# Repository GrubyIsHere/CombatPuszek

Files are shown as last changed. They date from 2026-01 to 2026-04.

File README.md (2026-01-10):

# CombatPuszek
Fancy combat-type robot with huge saw on top.

Angled version

Flattop version

## Features
*   ESP32-based remote control system.
*   All-around horizontal saw, up to 250mm in diameter.
*   3lbs (1.36kg) weight category.
*   Two drive configurations: wheels or soft tracks.
*   Swappable motor drivers, main ESC, and even main ESP32 module. 
*   Powered by 3S LiPO.

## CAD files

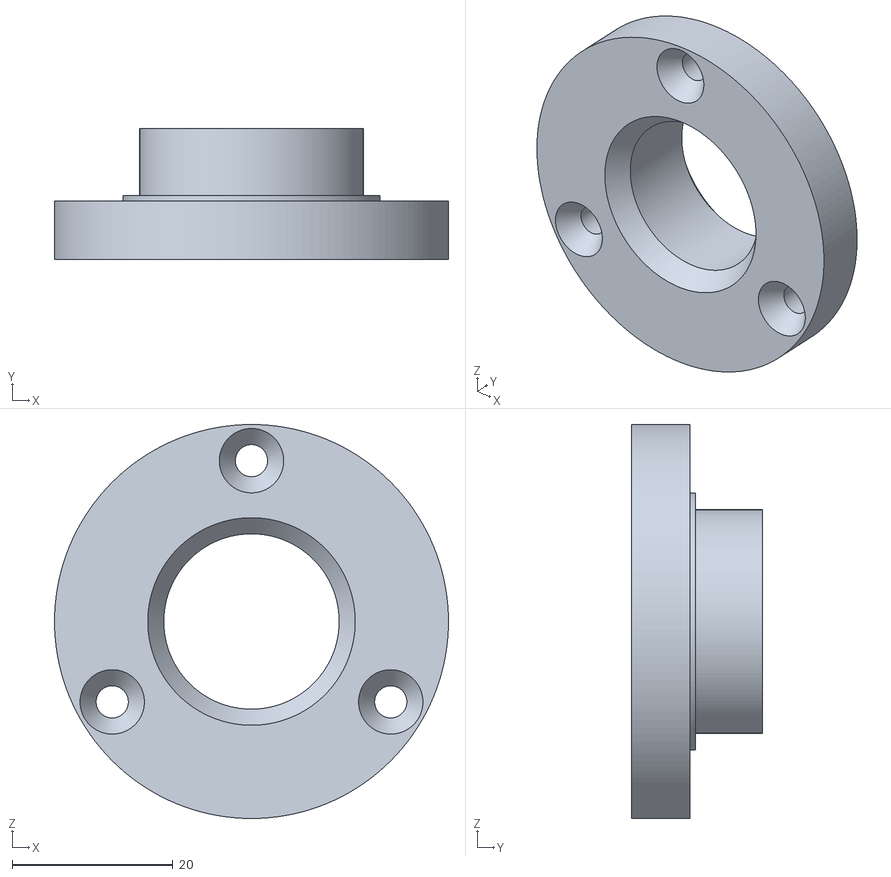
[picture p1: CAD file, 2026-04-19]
Mechanicals/mocowania_piły/nextgen_sidemount_alt_32mm - docisk_piły_fullprzelot.stl
49.0 x 16.2 x 49.0

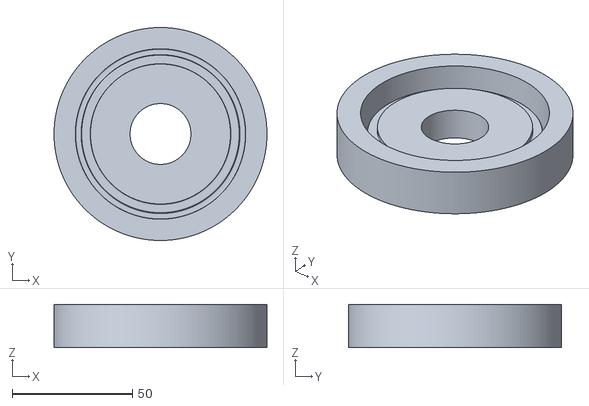
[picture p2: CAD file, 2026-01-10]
Mechanicals/koła_fi34/gąska dla kół fi34/baza_fi70,8.stl
88.5 x 88.5 x 18.0

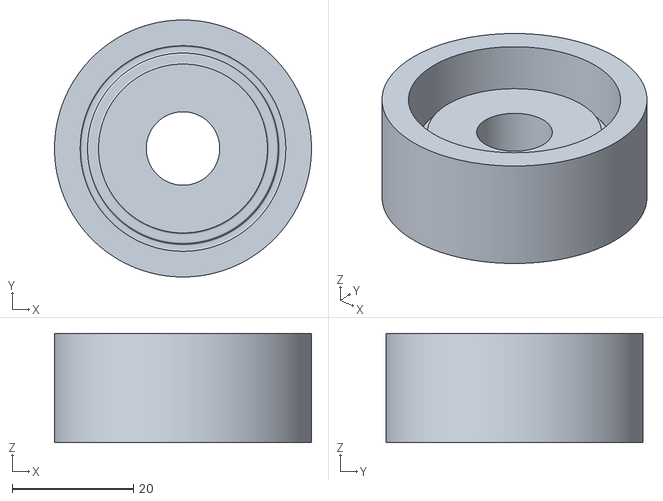
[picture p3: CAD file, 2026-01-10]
Mechanicals/koła_fi34/opona dla kół fi34/baza_fi34.stl
42.4 x 42.4 x 18.0

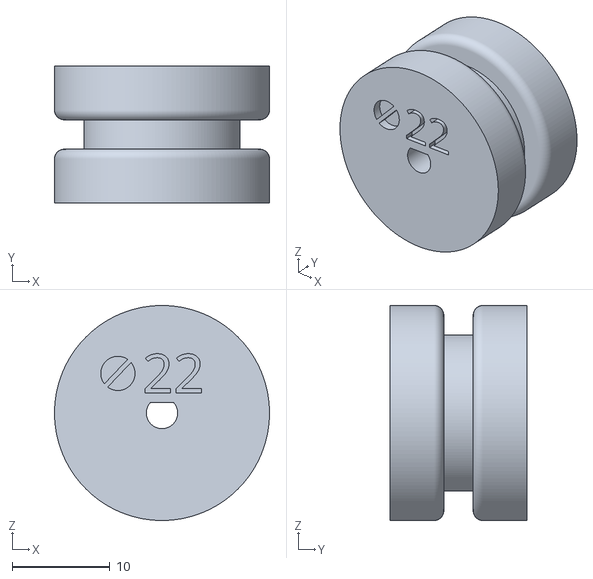
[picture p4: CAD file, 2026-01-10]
Mechanicals/koła_inne/puszkoło_fi22.stl
22.0 x 14.0 x 22.0

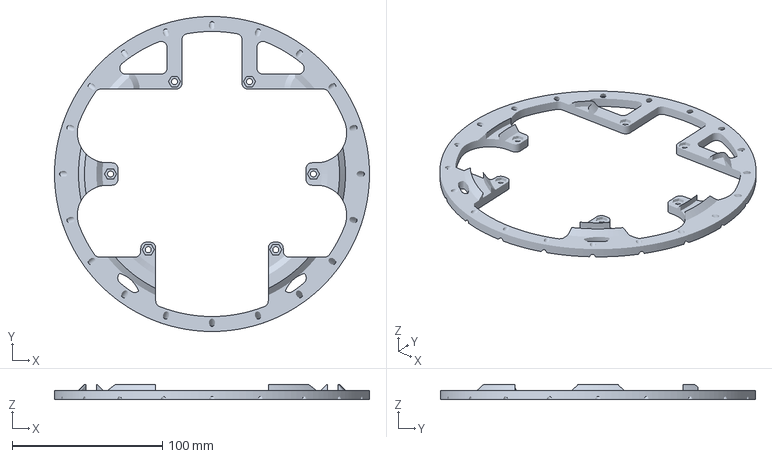
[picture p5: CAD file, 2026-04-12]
Mechanicals/kryzy/kryza_płaska_nextgen - dół.3mf
210.0 x 210.0 x 10.0 mm

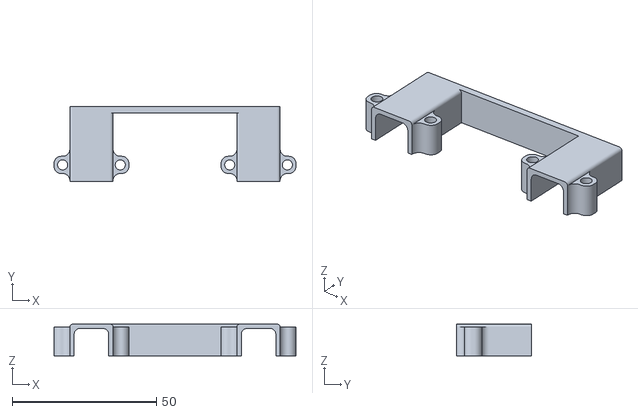
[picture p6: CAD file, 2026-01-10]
Mechanicals/mocowania_silników/doubleBracket_solid.stl
84.0 x 26.0 x 11.0

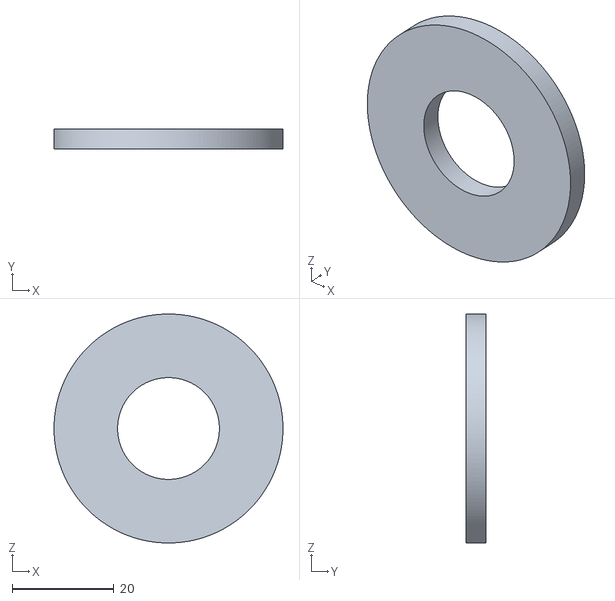
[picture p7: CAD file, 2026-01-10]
Mechanicals/podkładka_20x45x4mm.stl
45.0 x 4.00 x 45.0

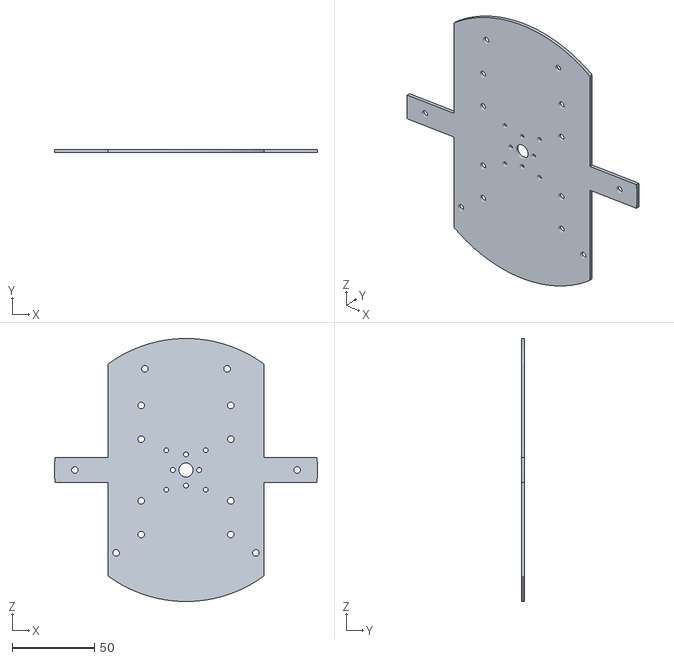
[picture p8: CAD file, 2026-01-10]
Mechanicals/spody/matryca_spodu_wersja_lekka.stl
160.0 x 2.00 x 160.0

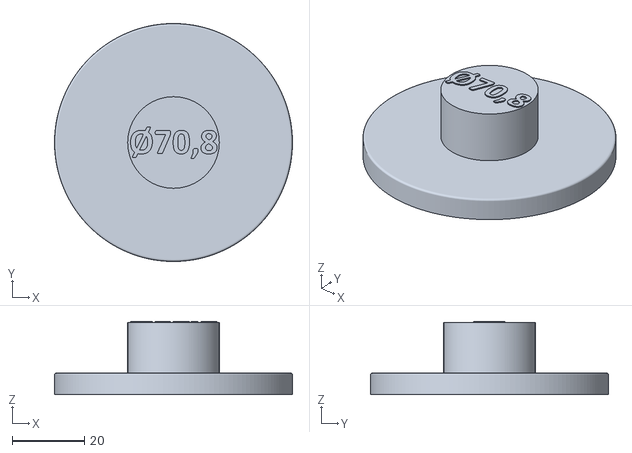
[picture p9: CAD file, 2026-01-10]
Mechanicals/koła_fi34/gąska dla kół fi34/korek_fi70,8.stl
65.7 x 65.7 x 20.3

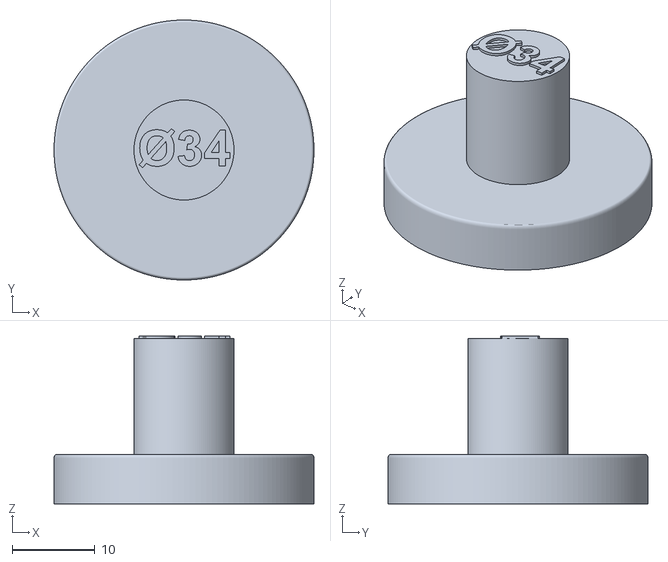
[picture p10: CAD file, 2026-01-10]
Mechanicals/koła_fi34/opona dla kół fi34/korek_fi34.stl
31.5 x 31.5 x 20.3

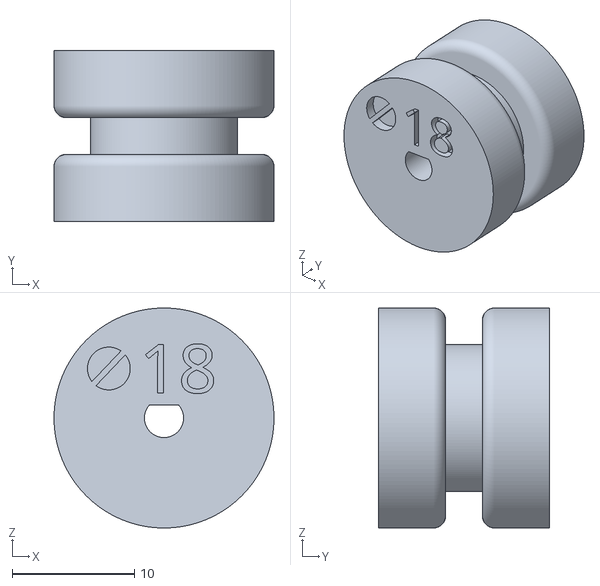
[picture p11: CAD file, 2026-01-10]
Mechanicals/koła_inne/puszkoło_fi18.stl
18.0 x 14.0 x 18.0

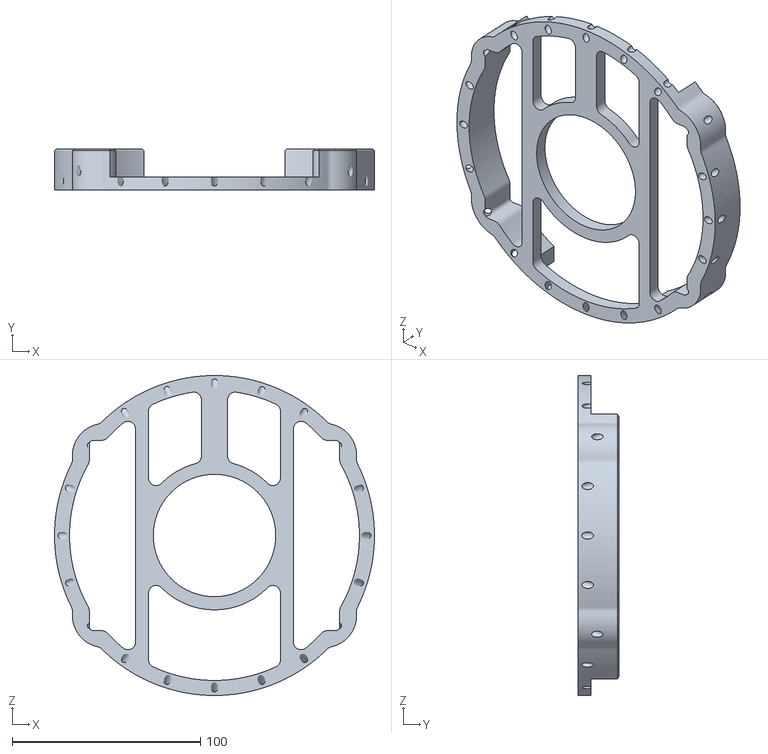
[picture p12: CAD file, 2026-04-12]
Mechanicals/kryzy/kryza_płaska_nextgen - góra.stl
170.0 x 22.0 x 170.0

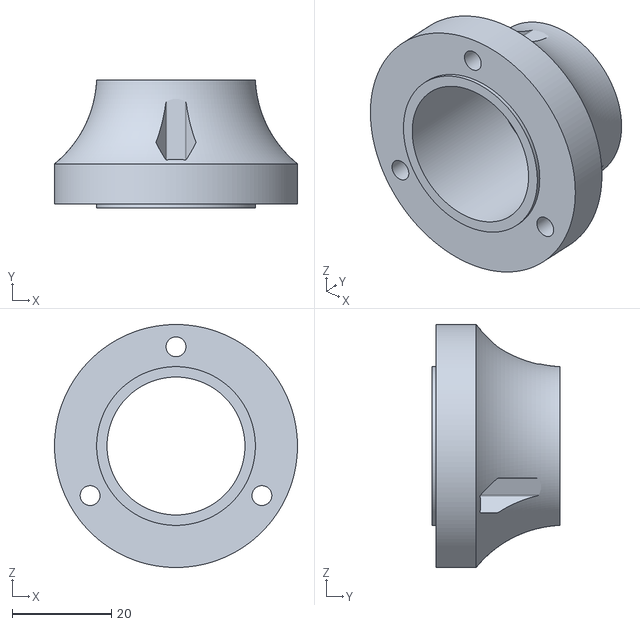
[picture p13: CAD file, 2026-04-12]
Mechanicals/mocowania_piły/nextgen_sidemount_32mm - łoże_piły.stl
49.0 x 25.8 x 49.0

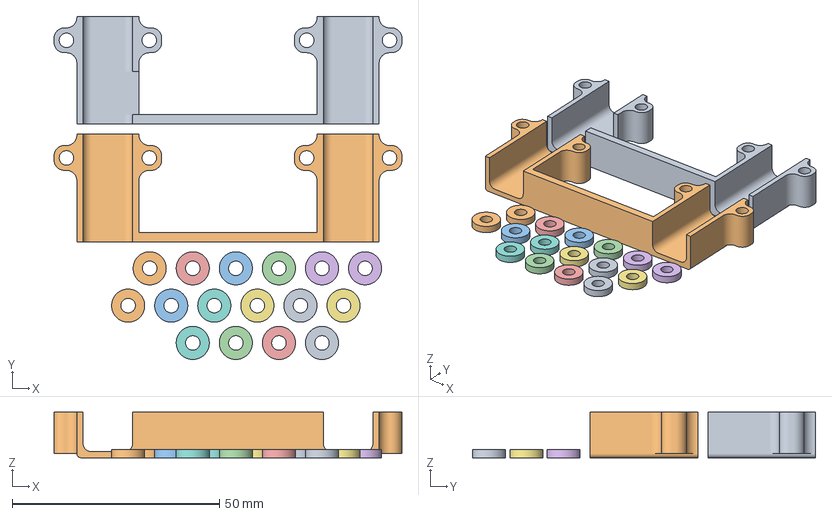
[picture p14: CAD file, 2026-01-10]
Mechanicals/mocowania_silników/mocowania_silników.3mf
84.0 x 82.8 x 11.0 mm
doubleBracket_cutted.stl
doubleBracket_solid.stl
podkładka_3.5x8x2mm.stl x 16

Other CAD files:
Mechanicals/podkładka_3.5x8x2mm.stl
Mechanicals/spody/puszek_blacha_plasticzanowa_gruba.step
Mechanicals/koła_inne/fi34.stl
Mechanicals/kryzy/kątokryza_13st.stl
Mechanicals/koła_inne/fi28.stl
Mechanicals/koła_inne/puszkoło_fi20.stl
Mechanicals/koła_inne/puszkoło_fi24.stl
Mechanicals/kryzy/kryza_płaska_OLD.stl
Mechanicals/kryzy/kryza_płaska_nextgen - dół.stl
Mechanicals/kryzy/kątokryza_10st.stl
Mechanicals/mocowania_piły/kątownik_piły_10st.stl
Mechanicals/mocowania_piły/kątownik_piły_13st.stl
Mechanicals/mocowania_piły/mocowanie_piły_górnodolne_multicentra_20mm.stl
Mechanicals/mocowania_piły/mocowanie_piły_górnodolne_multicentra_32mm.stl
Mechanicals/mocowania_silników/doubleBracket_cutted.stl
Mechanicals/spody/puszek_blacha_plasticzanowa_lekka.step

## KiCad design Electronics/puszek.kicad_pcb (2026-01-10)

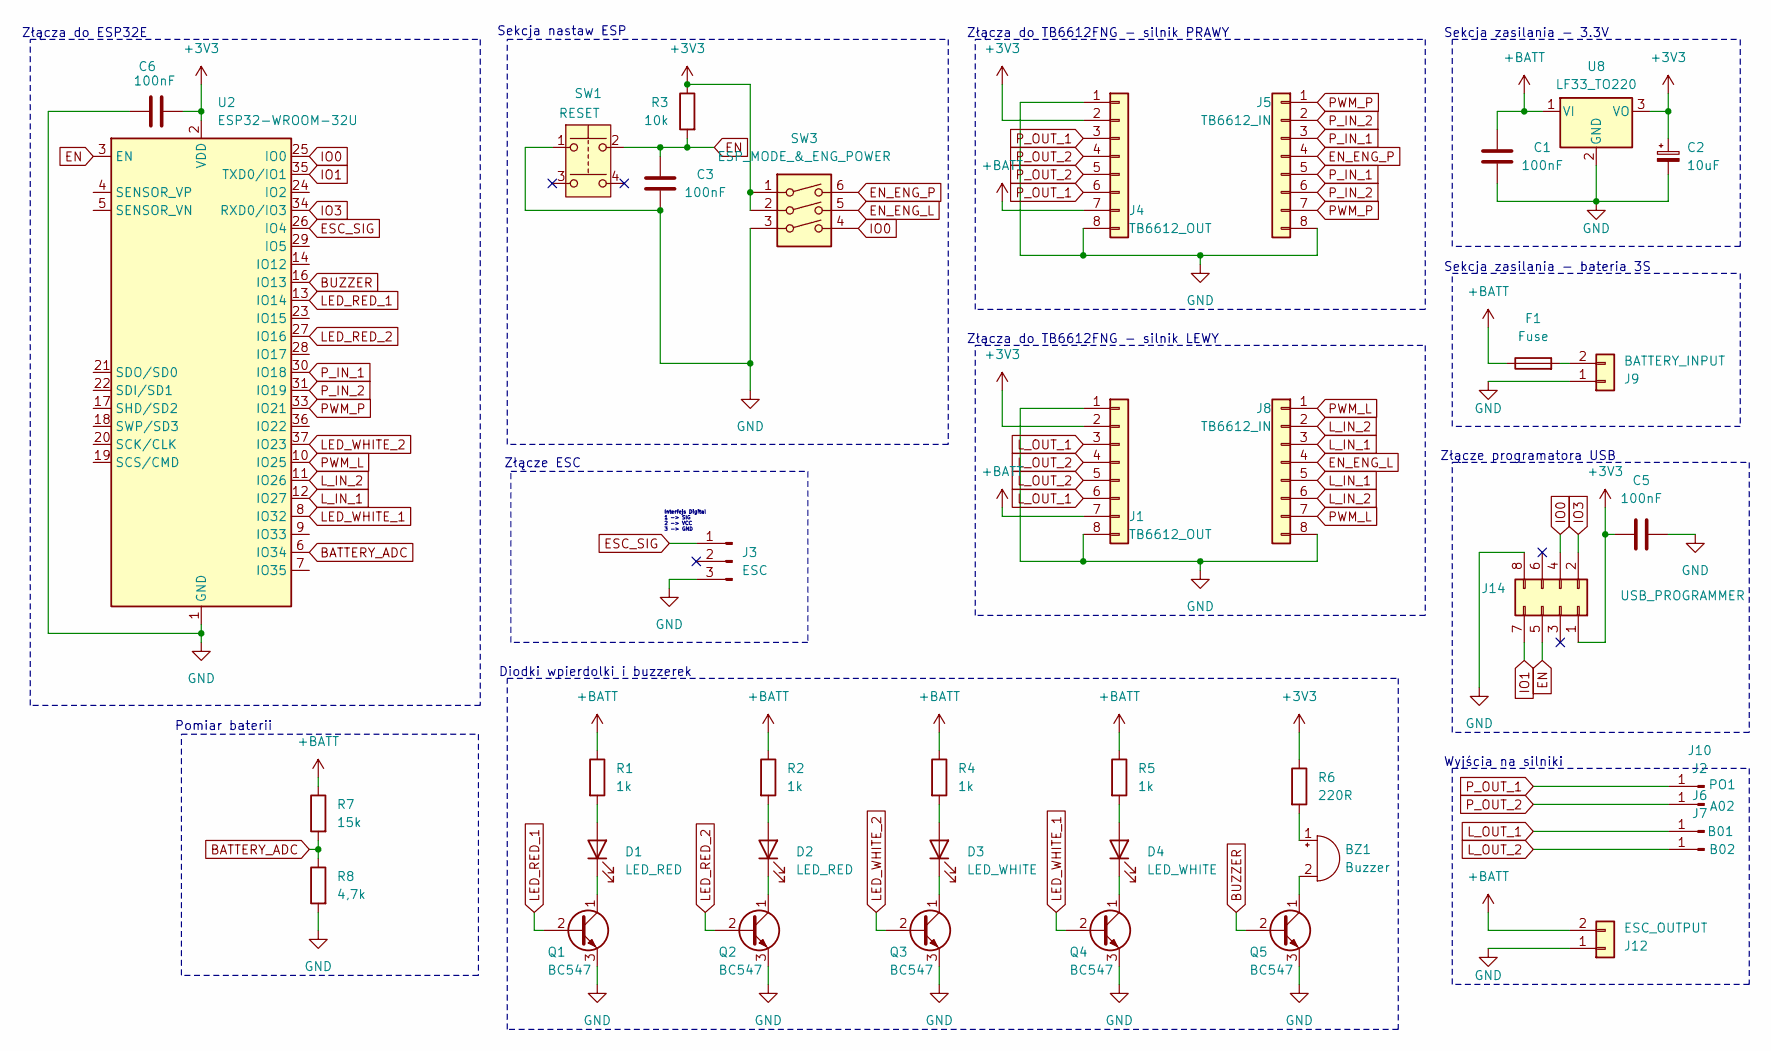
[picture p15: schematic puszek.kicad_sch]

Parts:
BZ1: Buzzer; Buzzer_12x9.5RM7.6
C1, C3, C5, C6: 100nF; C_0603_1608Metric
C2: 10uF; CP_Radial_D5.0mm_P2.50mm
D1, D2: LED_RED; LED_D5.0mm
D3, D4: LED_WHITE; LED_D5.0mm
F1: Fuse; Fuse_Littelfuse_395Series
J1, J4: TB6612_OUT; PinHeader_1x08_P2.54mm_Vertical
J2: A02; PinHeader_1x01_P2.54mm_Vertical
J3: ESC; PinHeader_1x03_P2.54mm_Vertical
J5, J8: TB6612_IN; PinHeader_1x08_P2.54mm_Vertical
J6: B01; PinHeader_1x01_P2.54mm_Vertical
J7: B02; PinHeader_1x01_P2.54mm_Vertical
J9: BATTERY_INPUT; AMASS_XT60-F_1x02_P7.20mm_Vertical
J10: PO1; PinHeader_1x01_P2.54mm_Vertical
J12: ESC_OUTPUT; AMASS_XT60-F_1x02_P7.20mm_Vertical
J14: USB_PROGRAMMER; PinHeader_2x04_P2.54mm_Vertical
Q1, Q2, Q3, Q4, Q5: BC547; TO-92_Inline
R1, R2, R4, R5: 1k; R_0603_1608Metric
R3: 10k; R_0603_1608Metric
R6: 220R; R_0603_1608Metric
R7: 15k; R_0603_1608Metric
R8: 4,7k; R_0603_1608Metric
SW1: RESET; SW_PUSH_6mm_H5mm
SW3: ESP_MODE_&_ENG_POWER; SW_DIP_SPSTx03_Slide_9.78x9.8mm_W7.62mm_P2.54mm
U2: ESP32-WROOM-32U; adapter_ESP32_NEW
U8: LF33_TO220; TO-220-3_Horizontal_TabDown

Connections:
+3V3: C2.1, C5.1, C6.1, J1.2, J4.2, J14.1, R3.1, R6.1, SW3.1, SW3.2, U2.2 (VDD), U8.3 (VO)
+BATT: C1.2, F1.1, J1.7, J4.7, J12.2, R1.1, R2.1, R4.1, R5.1, R7.1, U8.1 (VI)
BATTERY_ADC: R7.2, R8.1, U2.6 (IO34)
BUZZER: Q5.2 (B), U2.16 (IO13)
EN: C3.2, J14.5, R3.2, SW1.2, U2.3 (EN)
EN_ENG_L: J8.4, SW3.5
EN_ENG_P: J5.4, SW3.6
ESC_SIG: J3.1, U2.26 (IO4)
GND: C1.1, C2.2, C3.1, C5.2, C6.2, J1.1, J1.8, J3.3, J4.1, J4.8, J5.8, J8.8, J9.1, J12.1, J14.8, Q1.3 (E), Q2.3 (E), Q3.3 (E), Q4.3 (E), Q5.3 (E), R8.2, SW1.1, SW3.3, U2.1 (GND), U2.15 (GND), U2.38 (GND), U2.39 (GND), U8.2 (GND)
IO0: J14.4, SW3.4, U2.25 (IO0)
IO1: J14.7, U2.35 (TXD0/IO1)
IO3: J14.2, U2.34 (RXD0/IO3)
LED_RED_1: Q1.2 (B), U2.13 (IO14)
LED_RED_2: Q2.2 (B), U2.27 (IO16)
LED_WHITE_1: Q4.2 (B), U2.8 (IO32)
LED_WHITE_2: Q3.2 (B), U2.37 (IO23)
L_IN_1: J8.3, J8.5, U2.12 (IO27)
L_IN_2: J8.2, J8.6, U2.11 (IO26)
L_OUT_1: J1.3, J1.6, J6.1
L_OUT_2: J1.4, J1.5, J7.1
unnamed: BZ1.1 (+), R6.2
unnamed: BZ1.2 (-), Q5.1 (C)
unnamed: D1.2 (A), R1.2
unnamed: D1.1 (K), Q1.1 (C)
unnamed: D2.2 (A), R2.2
unnamed: D2.1 (K), Q2.1 (C)
unnamed: D3.2 (A), R4.2
unnamed: D3.1 (K), Q3.1 (C)
unnamed: D4.2 (A), R5.2
unnamed: D4.1 (K), Q4.1 (C)
unnamed: F1.2, J9.2
PWM_L: J8.1, J8.7, U2.10 (IO25)
PWM_P: J5.1, J5.7, U2.33 (IO21)
P_IN_1: J5.3, J5.5, U2.30 (IO18)
P_IN_2: J5.2, J5.6, U2.31 (IO19)
P_OUT_1: J4.3, J4.6, J10.1
P_OUT_2: J2.1, J4.4, J4.5

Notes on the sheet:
Sekcja zasilania - bateria 3S
Pomiar baterii
Wyjścia na silniki
Interfejs Digital 1 -> SIG 2 -> VCC 3 -> GND
Złącza do TB6612FNG - silnik LEWY
Złącza do ESP32E
Złącze programatora USB
Złącza do TB6612FNG - silnik PRAWY
Sekcja nastaw ESP
Złącze ESC
Sekcja zasilania - 3.3V
Diodki wpierdolki i buzzerek

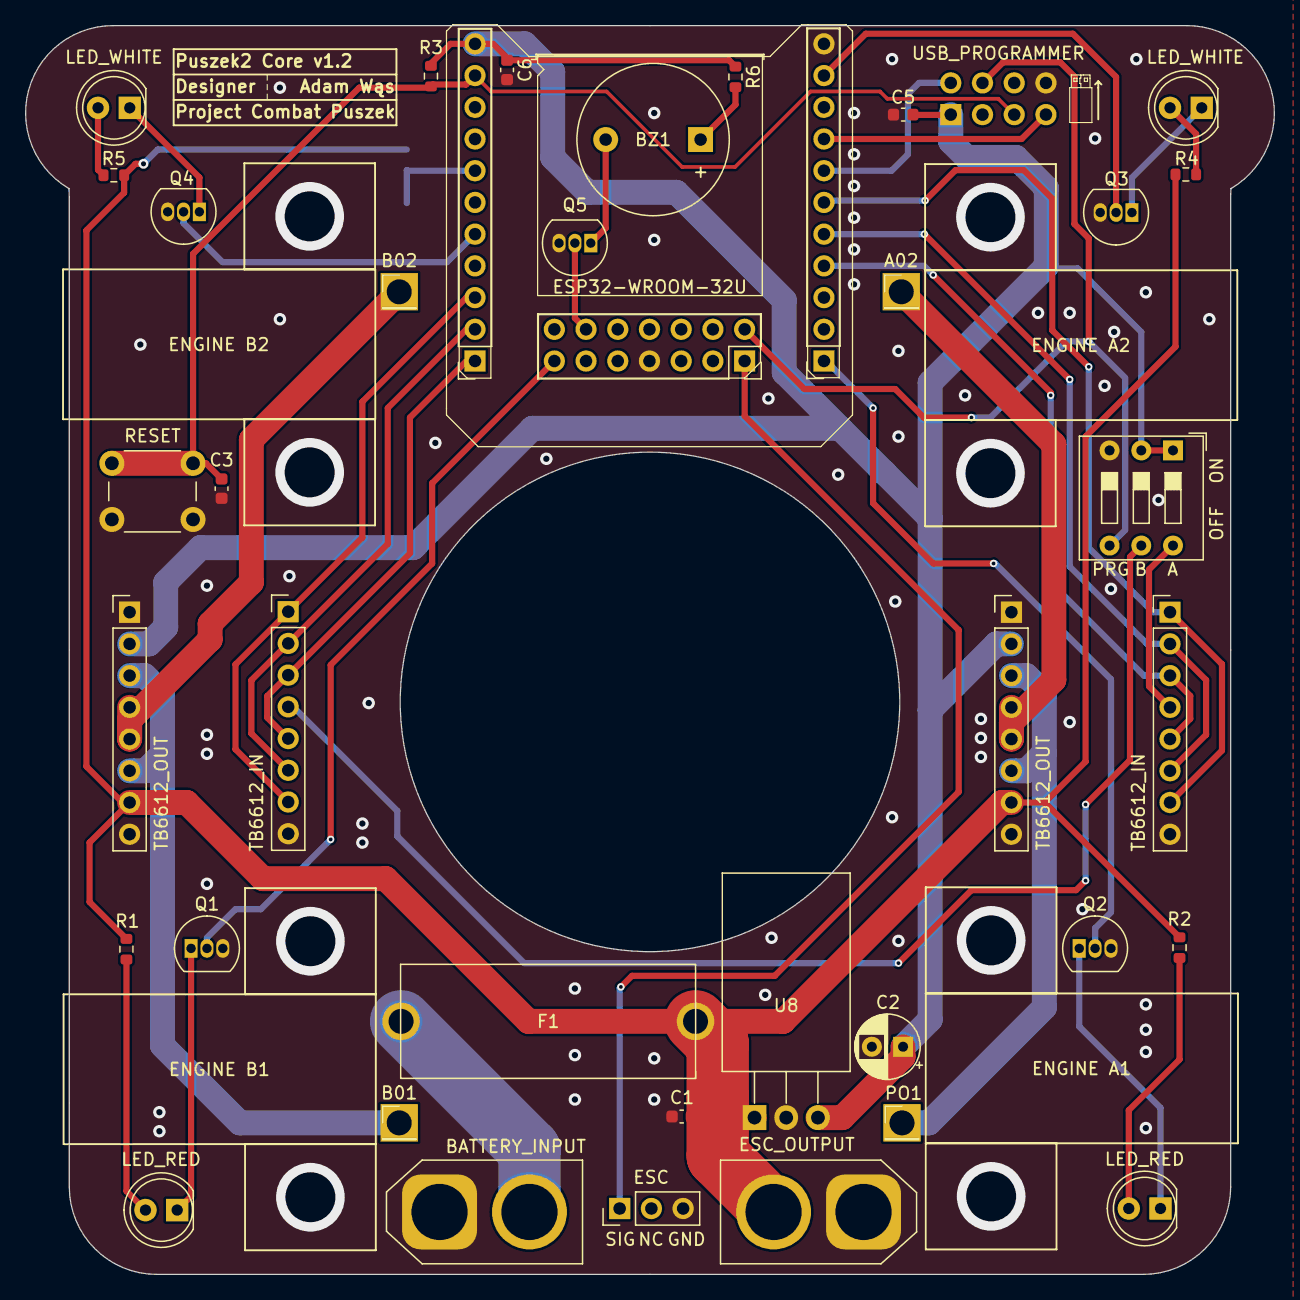
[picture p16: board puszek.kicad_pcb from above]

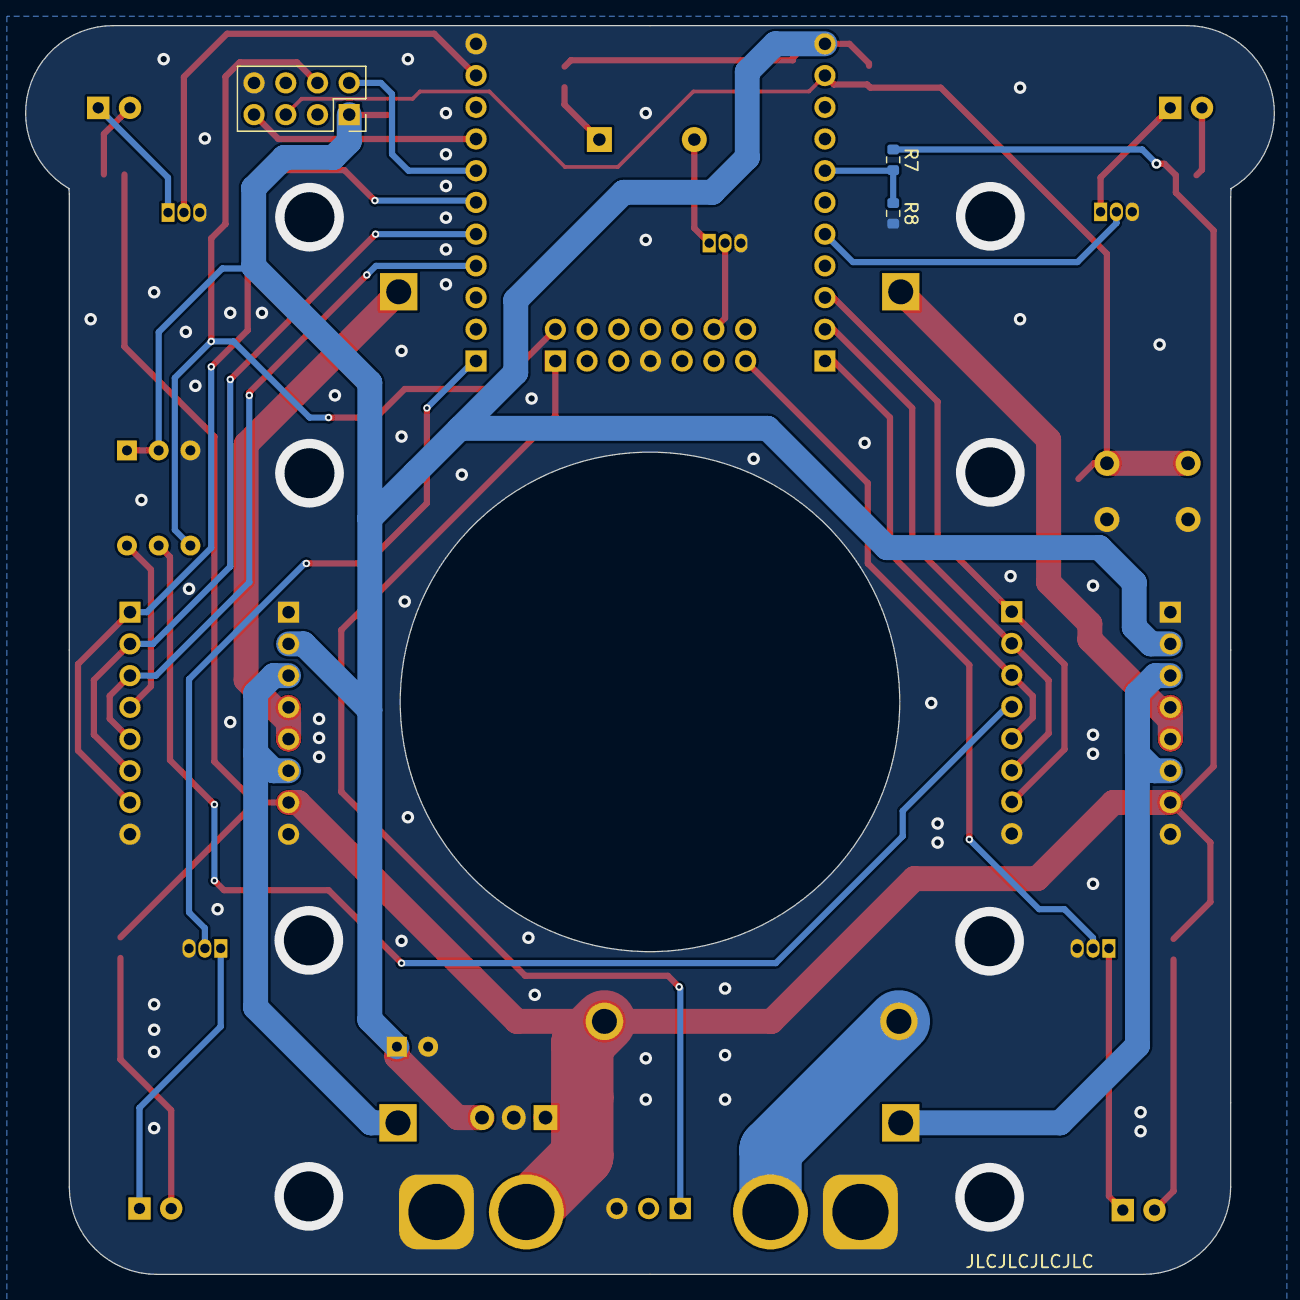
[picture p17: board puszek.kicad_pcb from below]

Board: 2 copper layers, 100.0 x 100.0 mm, 40 parts (2 on the bottom side), 37 nets.

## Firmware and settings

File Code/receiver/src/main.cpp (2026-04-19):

#include <A_Robot.h>
#include <K_ESPNOW.h>
#include <Arduino.h>

K_ESPNOW E;
A_Robot R;

void setup() {
  // Serial Monitor DEBUG
  Serial.begin(115200);
  Serial.println("predone");

  E.Init();

  Serial.println("done");
}

void loop() {

  E.UpdateConnectionState();

  R.ManualControl();

// debug
  Serial.println(E.control.brake);
  Serial.println(E.control.connected);
  Serial.println(E.control.saw);
  Serial.println(E.control.speed_left);
  Serial.println(E.control.speed_right);
  // delay(1000);
}

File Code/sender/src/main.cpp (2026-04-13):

#include <Arduino.h>
#include <K_ESPNOW.h>
#include <S_Buttons.h>

// Complete project details at https://RandomNerdTutorials.com/esp-now-esp8266-nodemcu-arduino-ide/
K_ESPNOW E;
S_Buttons B;

// do timingu połączenia (musi być globalne)
unsigned long lastTime = 0;  
unsigned long interval = 1;

void setup()
{
  E.Init();

  // Serial.begin(115200);
  // Serial.println("done");
}

void loop()
{
  // Serial.println("loopstart");

  if (B.GetState(B.POINTER))
  {
    E.control.speed_left = 100;
  }
  else if (B.GetState(B.RING))
  {
    E.control.speed_left = -100;
  }
  else
  {
    E.control.speed_left = 0;
  }

  if (B.GetState(B.MIDDLE))
  {
    E.control.speed_right = 100;
  }
  else if (B.GetState(B.PINKY))
  {
    E.control.speed_right = -100;
  }
  else
  {
    E.control.speed_right = 0;
  }
  E.control.saw = B.GetState(B.THUMB);
  // jak wciskamy wszystkie sterowania (z piłą lub bez) to brake
  E.control.brake = B.GetState(B.ALL);
  E.control.connected = true; //sprawdzenie stanu (powinno nadpisywać receiver na true)

  E.Send();

  //debug
  // Serial.println("beforesend");
  // Serial.println(E.Send());
  // Serial.println("loopend");
  // Serial.println("Bool send: ");
  // Serial.println(E.control.brake);
  // Serial.println(E.control.connected);
  // Serial.println(E.control.saw);
  // Serial.println(E.control.speed_left);
  // Serial.println(E.control.speed_right);
  // delay(1000);
}

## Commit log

2026-01-10 initial full send
    [baza_fi34.stl, baza_fi70,8.stl, doubleBracket_cutted.stl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]
2026-04-12 minor code and mechanical changes
    [kryza_płaska_OLD.stl, kryza_płaska_nextgen - dół.3mf, kryza_płaska_nextgen - dół.stl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]
2026-04-13 communication timings fixes
    kod do wysyłania/odbierania sterowania działa teraz dużo lepiej
    [K_ESPNOW.cpp, main.cpp]
2026-04-19 minor connectivity fixes + new saw bracket model
    [nextgen_sidemount_alt_32mm - docisk_piły_fullprzelot.stl]
